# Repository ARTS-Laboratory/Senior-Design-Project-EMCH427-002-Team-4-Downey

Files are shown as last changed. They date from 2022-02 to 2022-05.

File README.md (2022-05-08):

# Senior-Design-Project-EMCH427-002-Team-4-Downey
## Camera-in-the-loop for Additive Manufacturing System (CLAMS)

### Background:
#### The Adaptive Real-Time Systems Laboratory (ARTS-Lab) at the University of South Carolina is working to develop a system for fault detection in additive manufactured components, particularly those that use metal-based processes.  Optical systems that can detect and quantify the size and location of the melt-pool in real-time are instrumental to this work.

### Project Purpose: 
#### This project will develop and build a camera-in-the-loop system that will include the camera housing, data acquisition system, and real-time computing hardware to compute the size and location of the melt pool. The software to compute the melt pool size will be provided but the project team will be required to implement this on real-time hardware. Key components to be developed include camera housing, data acquisition systems, real-time processing kernels, and display systems.

### Project Goal:
#### •	The development of a Camera-in-the-loop for Additive Manufacturing System. 

### Project Deliverables:
#### •	A fully functional camera-in-the-loop system.
#### •	A detailed public Github page will be made public and students can show it in their job search.
#### •	Detailed documentation with a “quick start guide”, source code, and CAD files. 

### Project Final Report:
#### •	The fianl report for the CLAMS.

## [Hardware setup for CLAMS](CLAMS_Hardware)
### 1. A build plate designed to accomadate monitoring apparatus
### 2. Camera mount to house optical camera
### 3. FLIR BFS-U3-16S2M-CS optical camera
### 4. Real-Time target unit
### 5. Display

concept individual components


## [Software](CLAMS_Software)
### Software designed during the development of this project.

## [Images and Figures](CLAMS_Images_&_Figures)
### Images and figures collected from this project.

## [Relevant Literature](CLAMS_Relevant_Literature)
### Documents including reports, research papers, user manuals, ect.

## [Source Code](CLAMS_Source_Code)
### Kernel and application code.

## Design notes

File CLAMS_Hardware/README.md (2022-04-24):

# CLAMS Hardware Setup

## [Custom Camera Mount](Custom_Camera_Mount)
### Drawings, G-code, and CAD files
2022-04-23 (3)

## [FLIR Optical Camera](FLIR_BFS_U3_16S2M_CS)
### Datasheet
2022-04-23 (4)

## [SLM Printer](Metal_3D_printer)
### Onwer's Manual


## [Monitor](Monitor)
2022-04-23 (7)

## [Real-Time Target Machine](Real_Time_Target_Units)
### User's Manual
2022-04-23 (6)

## [Return to Main Readme](https://github.com/ARTS-Laboratory/Senior-Design-Project-EMCH427-002-Team-4-Downey#readme)

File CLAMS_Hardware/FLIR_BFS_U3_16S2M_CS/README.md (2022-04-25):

# Flir Camera
## [Return to Hardware Readme](https://github.com/ARTS-Laboratory/Senior-Design-Project-EMCH427-002-Team-4-Downey/tree/main/CLAMS_Hardware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)

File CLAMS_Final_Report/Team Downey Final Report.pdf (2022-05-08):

## Adaptive Real-Time Systems Laboratory (ARTS-Lab)

## Camera-in-the-Loop System for Additive Manufacturing

## EMCH 427-428 – 2021-2022

Team Members: Malichi Flemming, Braden Priddy, Tyler Owens, Saif Wilkes-Davis

Industry Sponsor: Dr. Austin Downey

Department of Mechanical Engineering University of South Carolina Columbia, SC 29201

### Table of Contents

I. Executive Summary

The Adaptive Real-Time Systems Laboratory is a research group at the University of South

Carolina that does interdisciplinary research. They want a product that does monitors and

collects data on a selective laser melting printer for research of a Ph.D. candidate.

The needs of The Adaptive Real-Time Systems Laboratory were determined by doing several

interviews with Austin Downey and Yangzhou Fu and touring the printer, and after detailed

analysis, it was determined that light spectrum, speed of data acquisition system, speed of code

execution, detecting melt pool and quantifying melt pool were critical to satisfying those needs.

It was furthermore determined that a product to satisfy their requirements would need to be able

to process 200 frames per second, be portable, have a user-friendly repository of work, and able

to accurately and reliably generate contours with area calculations. It was thus determined that

the product mission should be the ARTS-Lab at the University of South Carolina needs a vision

system that can accurately track, calculate the brightness, and area of the melting sputters during

the SLM (Selective Laser Melting) process while functioning in real-time.

Given the above requirements, multiple concepts were researched and considered, as described

in this report. The ultimate concept selected to best satisfy The Adaptive Real-Time Systems

Laboratory’s needs was a FLIR camera with a bandpass filter in conjunction with a laptop for

storing and displaying data and Speedgoat controller as a real time target for Simulink code to

process the images. Details related to concept selection and subsequent product architecture are

supplied.

Speed of computational system, visibility of melt pool, and the accurate translation of brightness

to contours with area and locations are critical to functionality, and detailed engineering analyses are provided, demonstrating how expected light spectrum and heat transfer of the from the laser

to the PLA housing were modeled, under conditions of heat generated by the laser, and the

design was optimized.

Parameters included the camera’s execution speed, the melt pool’s light spectrum accuracy, and

the code’s processing speed are high priorities for production of the product. Therefore, the

design was optimized for these parameters which consisted of measuring how pixel size affected

processing time and analyzing individual functions in the code.

The prototype was tested by assessing different image processing methods to optimize speed and

the melting pool’s true area, displaying parameters versus not displaying parameters, and frames

per second versus the size of melting sputter under conditions ranging from optimal to non-

optimal.

Economic analysis of the scope of expenses associated with development of the prototype

indicate that, for a $24,253.40 investment, The Adaptive Real-Time Systems Laboratory will

recover all costs within the first unit sold and start earning profit at the same time.

II. Background

The Adaptive Real-Time Systems Laboratory is an interdisciplinary research laboratory at

the University of South Carolina. It is focused on developing tools and solutions that enable

systems (e.g., mechanical systems, aerospace structures, and civil infrastructure) to adapt to their

environments in real-time. It was created by and is led by Dr. Austin Downey, a professor at the

University of South Carolina in the Mechanical Engineering Department.

Digital twins will be a major factor for manufacturing in Industry 4.0 to increase reliability

by allowing real-time corrections to a process. The ARTS-Laboratory, in partnership with the

Metal 3D Printing Laboratory operated by Dr. Lang Yuan, is working to reduce waste by

increasing the accuracy and repeatability of the Selective Laser Melting 3D printer at the McNair

Center.

As part of the digital twin for this project, a computer vision system will be used to monitor

the performance characteristics of the printing process. With this data, Yangzhou Fu, a Ph.D.

candidate under Dr. Downey, will be able to apply a machine learning process to better the

additive manufacturing process with an in-situ system.

III. Customer Needs

3.1 Introduction

Determining customer needs accurately is critical to have a well-defined scope and a successful

project. Dr. Austin Downey of the ARTS Laboratory at the University of South Carolina needs

an in-situ monitoring system of a selective laser melting printer. With the guidance of Yanzhou

Fu, a Ph.D. student at the ARTS Laboratory, a computer vision system was created. This will be

used and tested in conjunction with the printer found in the McNair Center at the University of

South Carolina that is under the purview of Dr. Lang Yuan. One of the goals mentioned by Dr.

Downey was for the project to be useable by other research groups and hopefully industry

groups. Ultimately, the vision system needs to track the sputters, also known as molten ejecta,

created by the rapid heat of the metal powder. This project is designed to be one half of a digital

twin to do real-time corrections to SLM processes to improve the reliability to make it a more

accepted and viable practice.

3.2 Methodology

Dr. Downey and Mr. Fu were interviewed to understand what they wanted from the project. This

was done over the span of a few weeks to see if the goal would change based on the input.

Additionally, research was performed by watching Georgia Institute of Technology videos to

help understand what problem was being approached since this was a new concept. Additionally,

research was done to determine how the printer worked so it could be determined where the issue

in printing most likely was. The McNair center was visited with Mr. Fu to see the printer and its current setup. Afterward, discussions were had to determine what needs were most relevant via a

voting system.

3.3 Interpretation of Needs

Table 1: Original client needs

Needs Group | Needs | Needs #
Camera/Vision System | The system needs to be able to house the existing cameras and other future potential cameras | 1
| The camera mount must be stable. | 2
| The camera system must have a consistent field of vision. | 3
| The cameras must have appropriate frames per second to keep up the SLM’s scanner speed. | 4
| The cameras must have a proper light spectrum to view the part and the melt pool while the printing is occurring. | 5
| The camera must be protected | 6
DAQ/ Controller | The data acquisition system must be able to interface with available USB cameras as well as other commonly used USB camera systems. | 7
| The data acquisition system must be compatible with a real time system or fast enough to keep up with the cameras. | 8
| The data acquisition system must be cost effective. | 9
| The data acquisition system must be self-contained and portable. | 10
Code | The code must be executed fast enough | 12
| The code must be able to find the melt pool and outline the print area. | 13
| The code must be able to quantify melting pool area and sputters. | 14
| The code must track the x,y position of the melt pool | 15
| The code must have adequate documentation for future users. | 16
| The code must be able to display important parameters to the end user. | 17
Future Use/ Documentation | The system must come from existing equipment or 3D printed parts. | 18
| The system must have a repository for explaining how the system works. | 19
| The system must have a friendly GUI. | 20
| The documentation must be easy to use from technically literate people. | 21

Computer vision systems are made of several components such as image sensors, lens, vision

processor, communication interface, and lighting. The vision system consists of a camera and a custom holder to fulfill the image sensor and lens requirements. The data acquisition system

consists of a speed goat controller that handles the vision processing and communication aspects

of the design. Lastly, the lighting is created by the laser, melt pool, and plasma, and is filtered

using a bandpass filter. Each of the elements is broken out by subcomponent.

Needs Explanation:

1. The system needs to be able to house the existing cameras and other future potential cameras - To reduce cost, the use of existing equipment is a consideration.
2. The camera mount must be stable - To avoid vibrations from people walking nearby, the system needs to be held in place.
3. The camera system must have a consistent field of vision - The camera needs to see the same area in a repeatable fashion
4. The cameras must have appropriate frames per second to keep up the SLM’s scanner speed – The system needs to process frames at a set interval such that the distance the laser moves does not exceed a critical dimension length
5. The cameras must have a proper light spectrum to view the part and the melt pool while the printing is occurring – The camera must be able to see relevant aspects of the printing process
6. The camera must be protected - The system must be able to be reused for multiple other projects
7. The data acquisition system must be able to interface with available USB cameras as well as other commonly used USB camera systems – Dr. Downey has a FLIR USB camera that would be a preference for the system
8. The data acquisition system must be compatible with a real time system or fast enough to keep up with the cameras - The camera needs to see enough information fast enough to give accurate data on the melt process
9. The data acquisition system must be cost effective – Camera systems already exist, this system needs to save the ARTS laboratory money
10. The data acquisition system must be self-contained and portable – This product is a temporary addition to the SLM printer. It must be able to be removed and placed back again.
11. The code must be executed fast enough - The code must not prevent the camera system from achieving an appropriate speed
12. The code must be able to find the melt pool and outline the print area - The system needs a parameter to track for predictions later. By finding the melt pool and outlining it, it is possible to judge the consistency of the melting process and find deviations.
13. The code must be able to quantify melting pool area and sputters - The sputters, also known as molten ejecta, are a major source of defects in the printing process. Tracking their existence and size may make it possible to predict and eliminate them.

14. The code must track the x,y position of the melt pool - The code must be able to determine the location of the pool for reference of size later to improve the accuracy of the data by correcting locations relative to the camera
15. The code must have adequate documentation for future users – CAD and code must be available
16. The code must be able to display important parameters to the end-user - The end-user should be able to track the performance and correlate it to the printed quality.
17. The system must come from existing equipment or 3D printed parts – To save cost in a one-off prototype, the sponsor needs the part to be inexpensively made and customizable using resources available in the ARTS laboratory
18.  The system must have a repository for explaining how the system works – To make future work easier, code, instruction, CAD files, and other documents relevant to the project.
19. The system must have a friendly GUI – The end-user needs to be able to assess what is happening
20. The documentation must be easy to use for technically literate people- The end documentation must be accessible to those likely to use it

3.4 Prioritization of Needs

To determine the most important needs, a voting system [Table 2] was implemented. The

most important of the needs were given a four, the next most important given a two, marginally

important given a one, and the least important needs are given a zero. The total that must be

spent by each member is forty-eight.

Table 2: Point interpretation

Score | Interpretation
0 | Minimal Needed
1 | Marginally Important Need
2 | Mostly Needed
4 | Most Important
Must Spend | 48

Table 3: Affinity diagram

Needs # | Tyler | Malichi | Saif | Braden | Total | Rank
1 | 2 | 2 | 2 | 1 | 7 | 13
2 | 1 | 4 | 2 | 4 | 11 | 8
3 | 4 | 2 | 2 | 2 | 10 | 9

4 | 2 | 2 | 2 | 1 | 7 | 13
5 | 4 | 4 | 4 | 4 | 16 | 1
6 | 2 | 2 | 2 | 2 | 8 | 11
7 | 4 | 2 | 4 | 4 | 14 | 6
8 | 4 | 4 | 4 | 4 | 16 | 1
9 | 2 | 2 | 2 | 2 | 8 | 11
10 | 0 | 1 | 1 | 1 | 3 | 18
12 | 4 | 4 | 4 | 4 | 16 | 1
13 | 4 | 4 | 4 | 4 | 16 | 1
14 | 4 | 4 | 4 | 4 | 16 | 1
15 | 4 | 4 | 4 | 2 | 14 | 6
16 | 1 | 1 | 2 | 2 | 6 | 16
17 | 2 | 2 | 2 | 4 | 10 | 9
18 | 0 | 0 | 0 | 1 | 1 | 20
19 | 1 | 1 | 1 | 1 | 4 | 17
20 | 2 | 2 | 2 | 1 | 7 | 13
21 | 1 | 1 | 0 | 0 | 2 | 19
Individual Total | 48 | 48 | 48 | 48 | 192

Table 4: Top five results of first vote

Needs # | Tyler | Malichi | Saif | Braden | Total | Rank
5 | 4 | 4 | 4 | 4 | 16 | 1
8 | 4 | 4 | 4 | 4 | 16 | 1
12 | 4 | 4 | 4 | 4 | 16 | 1
13 | 4 | 4 | 4 | 4 | 16 | 1
14 | 4 | 4 | 4 | 4 | 16 | 1

Top Five Needs:

1. The cameras must have a proper light spectrum to view the part and the melt pool while the printing is occurring.
2. The data acquisition system must be compatible with a real-time system or fast enough to keep up with the cameras.
3. The code must be executed fast enough
4. The code must be able to find the melt pool and outline the print area
5. The code must be able to quantify melting pool area and sputters

Issue: While a top five was determined [Table 4], it was determined in the first round of voting

[Table 3]. This does not meet the requirements of a multiple voting process. There is a fair amount of overlap in the client's needs beyond the top five and the top five fail to consider the

full scope of the needs of the sponsor. Therefore, additional needs were generated by combining

other high-ranking needs and appending them to the top five. The most important needs after

modifications, voting, and discussions with the sponsor are seen below.

Vision System
1. The camera system must have a consistent field of vision - To make the product as reliable as possible, it is important that the edges of the images be consistent, so pixels represent the same space.
2. The cameras must have a proper light spectrum to view the part and the melt pool while the printing is occurring – For the system to work optimally, it is important to ignore extraneous sources of light.

Data Acquisition System
3. The data acquisition system must be self-contained and portable – This product is a temporary addition to the SLM printer. It must be able to be removed and placed back again.

Code
4. The code must be executed fast enough.  .5 ms (Allows for 200fps: Camera Max 226) -The system needs to track the rapid emissions of molten ejecta created by the laser heating process. The laser has a maximum travel speed of 2 meters per second. That means in one frame, the laser can travel up to 1 mm which may be a critical for tolerances depending on the application.
5. The code must be able to find the melt pool and outline the print area - The system needs a parameter to track for predictions later. By finding the melt pool and outlining it, it is possible to judge the consistency of the melting process and find deviations.
6. The code must be able to quantify melting pool area and sputters - The sputters, also known as molten ejecta, are a major source of defects in the printing process. Tracking their existence and size may make it possible to predict and eliminate them.
7. The code must be able to display important parameters to the end-user - The end-user should be able to track the performance and correlate it to the printed quality.

Future Use/Documentation
8.  The system must have a repository for explaining how the system works – To make future work easier, code, instruction, CAD files, and other documents relevant to the project.

### 3.5 Mission Statement

The ARTS-Lab at the University of South Carolina needs a vision system that can accurately

track, calculate brightness, and area of the melting sputters during the SLM (Selective Laser

Manufacturing) process while functioning in real-time.

IV. Specifications

### 4.1 Introduction

After the needs of the client were acquired over the course of several meetings with the

sponsor Dr. Downey and his Ph.D. student Yanzhou Fu. These needs went through three sets of

modifications as new information was exposed or issues arose. The list of client needs was

reduced to only the most vital 8. The needs were finalized after several rounds of voting using

scores ranging from 0-2.

After establishing and confirming the needs with the client, a needs metrics matrix was

crafted to help quantify the success throughout the project. Each of the client's needs is weighted

by importance based on the prior ranking of needs. For the needs metric matrix, a scale of 0, 1, 3,

and 9 was used. This was to emphasize items of utmost importance by using an exponentially

increasing ranking system adding more variance and preventing mass tying. The scale was in

ascending order of importance such that 0 had no importance and 9 had the most.

During this process, research was conducted to help generate specifications. Similar

research was found and used to find possible values for comparison. Most of the specifications

came from Dr. Downey and Mr. Fu. Beyond just setting specifications for the project to be

considered a success, fallback specifications were established to keep into account the wide

range of values that would arise as a result of the research-based environment of the project.

### 4.2 Metrics Table

Table 5: Metric table with target and fallback values

Needs | Units | Target specs | Fallback | Reference
Needs to detect melting pool (brightness) | Brightness | 0-255 | 0-255 | 3
Needs to detect melting pool (size) | Pixel value | Radius via contour | | 3
The cameras must have a proper light spectrum | Boolean | True positive | TP/TN | 6
Code must execute fast | ms | .5 | 33 | 3
Setup needs to be as compact and mobile as possible | cm^3 | 50 cm^3 | 100 cm^3 | 5
The code must be able to find the melt pool and outline the print area. | Boolean | True Positive | TP/TN | 5
The code must be able to display important parameters to the end-user | Boolean | True Positive | TP/TN | 5
The system must have a repository for explaining how the system works | Boolean | True Positive | TP/TN

Customer requirements/needs [Table 5] are in the leftmost column followed by the units used

to measure the need. Next are the target specs, which are the goals for the values attained. Fallback

values are acceptable values but not desired. Four client needs require true or false measurements, so

Boolean is the most often used metric for this project.

The idea of using a camera-in-the-loop system for detecting errors during an SLM (Selective

Laser Melting) process is a new idea that has been explored mostly by universities and research groups.

Because of the uniqueness of the idea, there are very few industry standards around the targets of the

project. Most of the target and fallback values are inferences made from other similar articles and

discussions with the project sponsors (Downey, Austin, and Yanzhou, Fu). These resources gave a good

idea of what the system’s target and fallback values should be in order to be successful.

### 4.3 Metrics Matrix

Table 6: Needs metrics matrix

The needs metrics matrix [Table 6] identifies the overall importance of each engineering

characteristic and ranks them in order of most important to least important. Out of the five engineering

characteristics, the most important has a ranking of one while the least important has a ranking of nine.

To determine these rankings, each customer need is assigned an importance weight factor from one to

five with five being the most important and one the least important. The table is set up to ascertain how

each engineering characteristic affects each customer requirement with values zero, one, three, and

nine representing a no, low, medium, and high correlation, respectively. From the results, it is

concluded that the Boolean metric ranks the highest, and the weight of the system ranks the lowest.

### 4.4 Outcomes

The client’s needs were taken and evaluated with the corresponding metrics and units using both

research and guidance from the project sponsors. After creating the two different tables above, a

clearer insight into the product's specific requirements was more readily attainable. Aside from the

Boolean metric, which is very generic, it was found that the two most essential engineering

characteristics were “the radius and brightness of the melting pool” and “processing time”. It was also

found that the “weight of the system” was the least necessary characteristic. The client requirement

that included the most engineering characteristics was the “the code must be able to find the melt pool

and outline the print area” with four correlations. The client requirement that included the least

engineering characteristics was the “the system must have a repository for explaining how the system

works” with one correlation. It was also determined the client's need with the most critical target and

fallback specification is the “need to detect melt pool (brightness)” and “code must execute fast” which

is appropriate, considering the two needs are the ultimate goal of the project.

V. Functional Concept

### 5.1 Introduction

The purpose of this chapter is to identify all functions of the vision tracking system.

Research was carried out on a variety of sources to develop a list of functions. From this list a

functional decomposition diagram was generated. A concept combination table was created by

researching and ideating a multitude of ways to execute each function. The Concept

Combination Table was then utilized to design five concepts that are applicable solutions for the

product. These concepts were analyzed and voted on to narrow down the options. These tools

were beneficial for understanding the problems that were faced and to develop a product that

fulfils the sponsor’s mission by choosing multiple solutions to answer these problems.

### 5.2 Functional Decomposition

A functional decomposition breaks down the product mission into detailed functions that

describe the problems that must be solved to build a successful vision tracking system. The

functions must consist of a verb and noun that answers the question, “what must this product

do,” to fulfill the product mission. Below is the detailed list of functions gathered for the

functional decomposition.

List of Functions
1. Locate Appropriate Camera Distance and Placement
2. Move Cameras into Position
3. Stabilize Camera System
4. Protect Camera from Heat, Molten Metal Sputters and Metal Powder
5. Operator determines Best Camera Settings
6. Set Camera Settings for Optimal Image Quality
- Set Camera to Correct Light Spectrum
- Set Resolution to Meet Image Quality Needs

- Set the Camera Frames Per Second to Meet Needs of Speed of the Printer
7. Accept External Energy from Power Source
8. Power Controller, Display, and Camera
9. Boot Real Time Operating System Initiating Tracking Program
10. User Inputs Command to Begin Tracking
11. Collect, Transfer, and Store/Buffer Images of Melting Pool from Camera to Data Acquisition System or Computer
12. Process the Images
13. Measure Radius and Luminance of Melting Pool

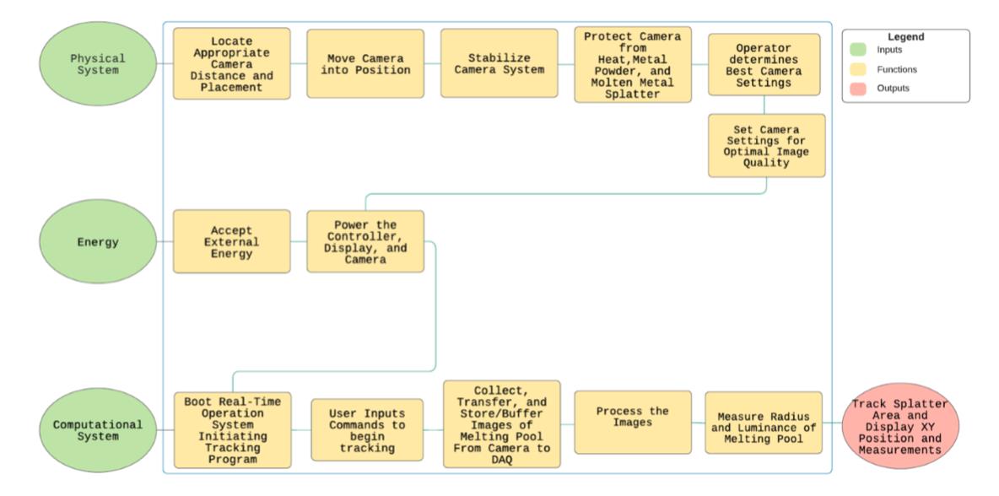
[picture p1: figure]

Figure 1: Function decomposition diagram

The diagram [Figure 1] functions as a visual representation of the required actions the

working product must implement to produce the desired outcome. The diagram consists of

inputs, functions, and outputs, flows primarily from left to right then secondarily from top to

bottom, and includes a color-coded legend for clarity. The inputs are the essential ingredients

needed to build the vision tracking system and the output(s) is the desired result of the fully

functioning product. The completed functional decomposition diagram can then be used to create

a concept combination table.

### 5.2 Concept Combinations

The Concept Combination Table (CCT) is a table that was generated using the functions

expressed in the Functional Decomposition Diagram. To formulate creative options, several

brainstorming and research sessions took place. In Table 7, each column of the CCT consists of a

heading that describes the function, and rows below containing all the feasible options that could

carry out the function.

Table 7: Concept Combination Table

Certain functions have only one logical option to fulfill it; however, additional options

were added for the sake of brainstorming and generating ideas. Functions such as “Boot the real-

time system” and “Move camera into position” would be done by hand. In principle,

accumulating these ideas assisted with future design concepts.

### 5. Concept Generation:

Concepts were generated by assigning one or more options from the Concept

Combination Table to each function and assembling the selected options into a viable concept.

Each team member assembled four concepts each totaling sixteen concepts, and the top five

concepts were chosen by vote. The following figures are illustrations of the chosen concepts

along with tables listing the technologies used for each function and brief explanations of how

the concepts work.

Table 8: Robot dog concept

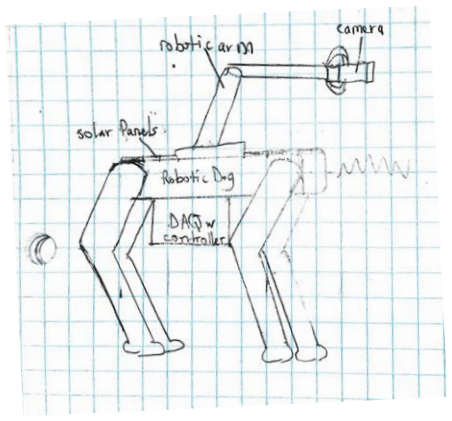
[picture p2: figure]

Figure 2: Robot dog concept hand drawing

In Figure 2, the Robot Dog concept uses a Boston Dynamic type robotic dog that is

powered by solar energy using solar panels placed along its back. The energy is stored in a built-

in battery that also powers the controller and camera. A robotic arm with a hand is attached to

the top of the robotic dog to hold, stabilize, and move the camera. A bright light-sensing camera

and C ++ software locate where to place the camera, sets camera settings, and processes the

images. The OpenCV function, calculate intersection(),a luminance meter records measurement,

and all data is stored on a hard drive disk. Desired output data is delivered via audio speaker

using text to speech application. Although the robot dog would be a creative idea, it would also

would very expensive, and solar power would not be effective indoors. Table 8 shows the

technology chosen for each function.

Table 9: Python application on laptop with SSK and heat-seeking camera concept

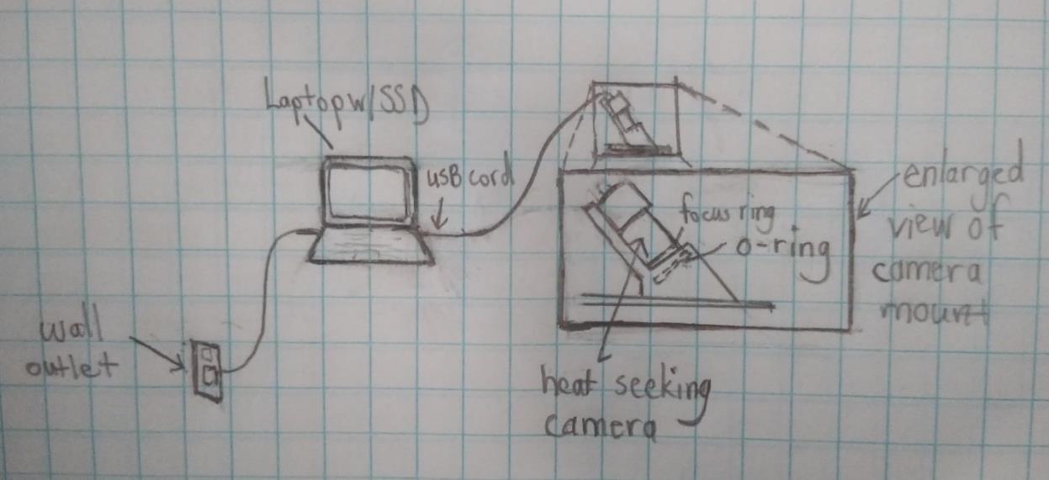
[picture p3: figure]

Figure 3: Laptop with SSD and Python concept

In Figure 3, a Python application that tracks the melting pool using a heat-seeking camera

will be executed on a laptop with SSD. The laptop is powered by a wall outlet and a USB cord

powers the camera and enables the transfer of data from the camera to the laptop. Focus rings

are manually added to focus the camera and a 3D printed camera holder with an O-ring stabilizes

and protects the camera. The laptop processes the data and displays the measurements on the

screen. This concept would be one of the most cost-efficient ideas and is the least complicated

which made it an ideal solution. Table 9 shows the technology chosen for each function.

Table 10: Robot arm with camera concept

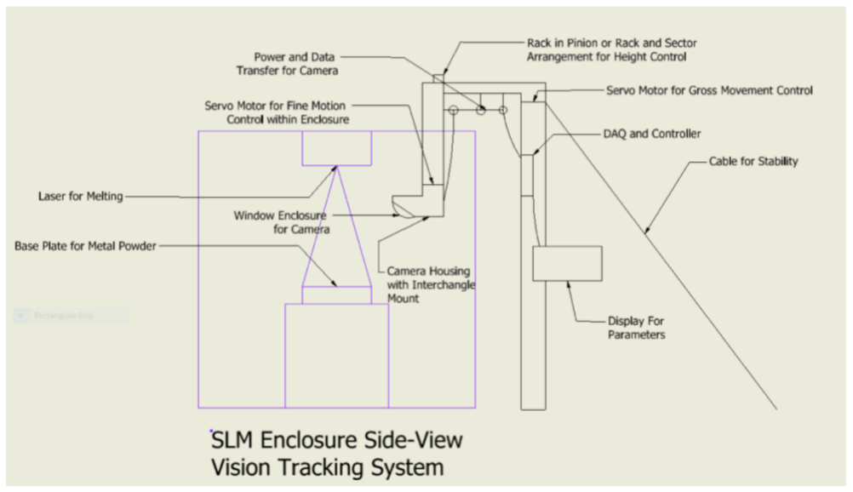
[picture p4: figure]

Figure 4: SCARA variant concept

In Figure 4, a robotic arm controls the positions of the camera within the enclosure. The

robot arm is designed to lift outside of the enclosure to allow for easy replacement of the

cameras as needed. The software takes into consideration the camera lens to determine the height

needed for optimal optics. To deal with the camera shaking during movements, a cable is added

to absorb some of the vibrations. A seal is formed with an O-ring and a 3D printed camera

housing to protect the cameras from harm. Power is supplied to the display, controller, and

motors from a 120 Volt outlet. The controller then powers the camera system. Once powered, the image will be processed in a real-time operating system running Python code. This code tracks

luminance to determine the melt pool position and splatter patterns.

This design is good because it can manipulate the camera into better angles than the

current mounting setup. The overall setup is inexpensive. The pole could be made of PVC or

wood and the motors harvested from equipment at a state surplus. The rest of it could be 3D

printed. Unfortunately, the complexity of the design would add more work to the project and add

cost to Dr. Downey. Additionally, it would need a secondary controller for the motor system.

Table 10 shows the technology chosen for each function.

Table 11:Manual control of system

Figure 5: Manual control of system

In Figure 5, the system is controlled primarily by the user. The camera is manually

adjusted using focus dials, and the user is holding the camera in the necessary location. The

camera is a heat-seeking camera therefore the printer has an open area to let heat out. However,

the user and the camera should not get overheated, so a fan is placed in the vicinity for cooling.

The user is also wearing a battery pack that is powering the system. Data is displayed on the TV

screen. This option is optimal for being able to control the system to the users' liking, however,

that means there must always be someone there during use. Table 11 shows the technology

chosen for each function.

Table 12: Remotely viewed data

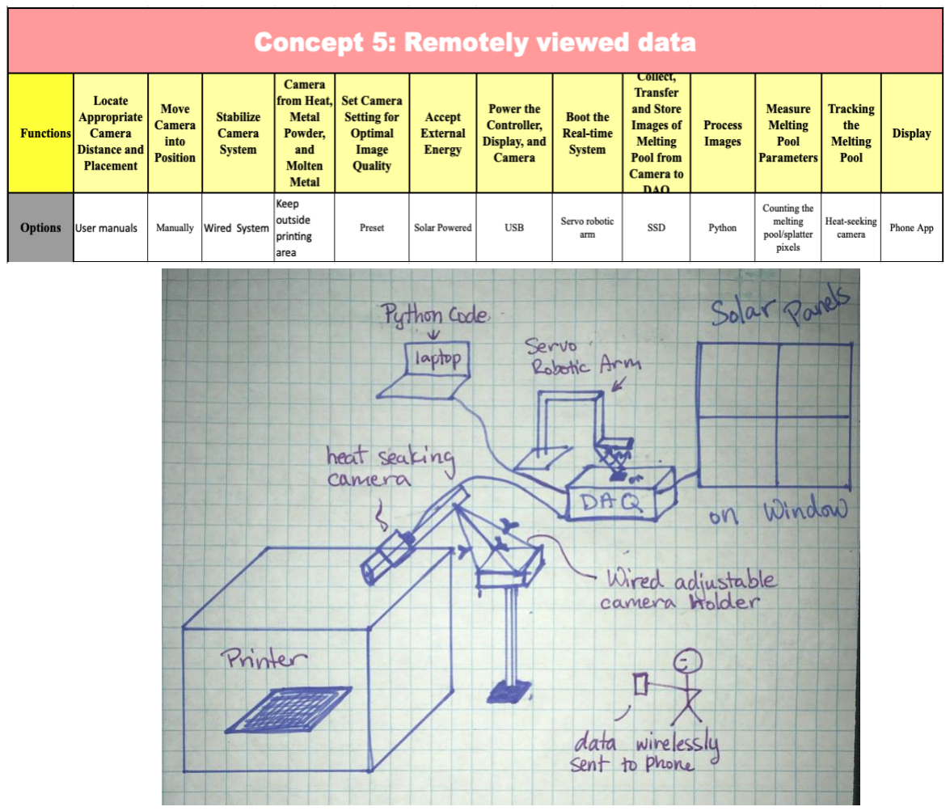
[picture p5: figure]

Figure 6: Remotely viewed data

In Figure 6, the camera is set up outside the printing area and held in place using an

adjustable wired setup. The system is booted using a remote-controlled servo arm and everything

is powered by solar panels attached to a nearby window. The data is configured using python

code and then wirelessly sent to the user’s phone via a cellphone application. The wired setup is

convenient since it can be adjusted to fit the apparatus, however, having data sent wirelessly to a

phone app gives opportunities for security violations. Table 12 shows the technology chosen for

each function.

### 5.3 Research performed

Patents were searched for under a couple of websites - Google patents [7] and United States

Patent and Trademark Office [8]. Keywords include the following:

- Metal 3-dimensional printer monitoring
- 3-dimensional printer monitoring
- 3-dimensional printer tracking
- Melting pool tracking
- Melting pool monitoring
- Monitoring of laser powder bed
- Selective laser melting
- Melting pool measurement
- Melting pool parameters
- Metal powder bed monitoring
•
There were few relevant patents to consider that were found using the above keywords

and that are cited in the appendix of this report. The first being the “Method and System for

Monitoring Additive Manufacturing Processes” [9] which is an invention that teaches quality

assurance for additive manufacturing using a multi-sensor and a real-time quality system.

Similarities include using multiple optical sensors to monitor the powder bed and using a real-

time operating system.

Another patent that is related to the project is one titled “Printer monitoring” [10] and is a

system that monitors 3D printers using a baseline image to compare to future images taken to determine the status of the print job and alert the user of any failures. This patent is not, however,

used with metal 3D printers, but collecting images to track data is similar to the project.

The last patent that was found that pertained to this project is the invention titled

“Procedure and apparatus for in-situ monitoring and feedback control of selective laser powder

processing” [11] which monitors and controls the Selective Laser Powder Processing by using a

scanning device to follow the laser beam as well as a detector that can capture electromagnetic

radiation emitted from movement on the powder surface. It also consists of an optical system to

follow the laser beam.

The idea of using a camera-in-the-loop system for detecting errors during an SLM

(Selective Laser Melting) process is a new idea that has been explored mostly by other

universities and research groups. As such many of the ideas rely heavily upon other journals of

other research groups.

The research article “Machine-Learning-Based Monitoring of Laser Powder Bed Fusion”

[12] was very constructive for the concept generation. This article is like what is being

accomplished in the project and has helped generate quite a few new options for the functions.

One idea extracted from this article is the use of angled mirrors to get a top-down view of the

metal powder bed [Figure 7].

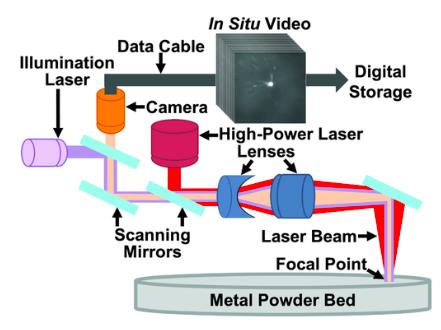
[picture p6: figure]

Figure 7: SLM video process

This idea can drastically simplify the project in two ways. With the use of mirrors, there is no

concern about varying camera angles and positioning; effectively eliminating two of the

functions (1. Locate Appropriate Camera Distance and Placement and 2. Move Cameras into

Position).

One important need of the sponsor is the software aspect. The product needs to be able to

track the 3D printing process and display the melting pool parameters all in real-time. This can

be difficult to code completely from scratch, so other ways to simplify this process were

researched. One way that was found was to use the OpenCV library [13]. Open Computer

Vision, “is an open-source computer vision and machine learning software library... that provides

a real-time optimized Computer Vision library, tools, and hardware [13].” OpenCV helped

generate options for two of the functions. The first function “12. Process the Images,” is done to

extract useful information from an image by modifying it. This can be accomplished almost exclusively by OpenCV functions. The image can be processed by multiple functions like

cvtColor(), GaussianBlur(), threshold(), erode(), and dilate(). All of which help the code find the

parameters of the melting pool. The second function OpenCV helped generate options for was,

“13. Measure Radius and Luminance of Melting Pool.” As shown in Figure 8, OpenCV has a

handy function called grab_contours(), which can draw a border around the melting pool.

Figure 8: Contour around the melting pool

Once this boundary is set, the melting pool’s parameters (centroid location, area, and radius) can

be calculated.

### 7. Conclusions:

All the designs share the project sponsor’s requirement that currently owned cameras

were used. This was important because there was a limited budget. Due to the nature of the

printer, it was important that the cameras were protected from heat and molten metal splatters.

One similarity between designs was that the camera was either outside of the printer enclosure or

protected with a casing if it was inside the enclosure.

One design limitation considered was that it needed to minimize the amount of human

interaction or manual work because there was not a budget for labor. Furthermore, there was

limited knowledge of robotics systems among the team working on the project so avoiding

complex solutions was necessary. Additionally, security concerns were considered because of the potential for confidential images of prototypes being made. The most complex functions to

solve were processing images or collecting and transferring images. This was because the coding

element for processing the images was successfully achieved in Python but needed to be

implemented in real-time.

VI. Concept Selection

### 6.1 Introduction

Project design is a strenuous and complex process for any engineering project. To

alleviate the difficulty of design selection, a variety of brainstorming methods were employed

which produced a multitude of designs. The brainstorming process began by listing the sponsor’s

needs to establish the desired parameters and a budget limit. Then the required functions of the

final design were listed, and a Functional Decomposition Diagram was constructed to help

illustrate how the design would work. For each of the functions, an extensive number of options

were produced. From these options, seven different designs were conceptualized enabling the

initiation of the Concept Design Review process. The first part of the process, Concept

Screening, involved narrowing down the concepts and deciding which ones could be combined

to create an optimal design concept. After narrowing down the seven concepts to three, the

second part of the process, Concept Ranking, began. Each of the three concepts were ranked by

weighing the sponsor’s needs to determine if the concepts could satisfy the design functions.

### 6.2 Concept Screening

Table 13: Initial concept screening

The selection criteria used for the concept screening were created and later updated after

meeting with the project sponsor. The criteria were adapted from the sponsor’s needs list as well

as the concepts that were designed. The concept screening [Table 13] was done by comparing the

reference concept, the original design endorsed by the sponsor, with the six novel concept

designs. The following symbols were used to rank the designs: a negative sign ‘-’ to represent

the design’s failure to meet the criteria as sufficiently as the reference design, a positive sign ‘+’

to represent the design successfully exceeding the reference design in meeting the criteria, and a

zero ‘0’ to represent the design matching the reference design’s ability to meet the criteria. The

reference design was given a zero for each of the criteria to provide a base level. The purpose of

using this type of concept screening was to rule out any designs that were not actually feasible

and to give the team an opportunity to take positive concepts from designs that didn’t rank very

high as a whole and piece them together to create a new combined design. The outcome of this concept screening took the team from the original 7 designs to 3 designs that include a

combination design.

### 6.3 Concept Ranking

Table 14: Final concept ranking

The concept ranking [Table 14] took place after determining the weights of the selection

criteria, a process that can be seen in the appendix. The criteria were compared to each other and

given a score of 1, 3, 5, 7, or 9 with a ranking of 1 having the lowest level of importance and 9

being much more important. Concept #2 (the reference concept) was the final selected concept

with the highest ranking. This was mainly due to the low budget available, and the simple setup

required. However, because concept #8 ranked so closely with the reference concept, a

discussion with the sponsor took place.

### 6.4 Final Concept

The final concept selected was concept #2, the reference concept, which is a python

application that tracks the melting pool splatter using an optical camera and executes on a laptop with a solid-state drive. Powered from a wall outlet, the laptop is then connected to the heat-

seeking camera via USB cable to power the camera and transfer data from the camera to the

laptop as seen in Figure 9.

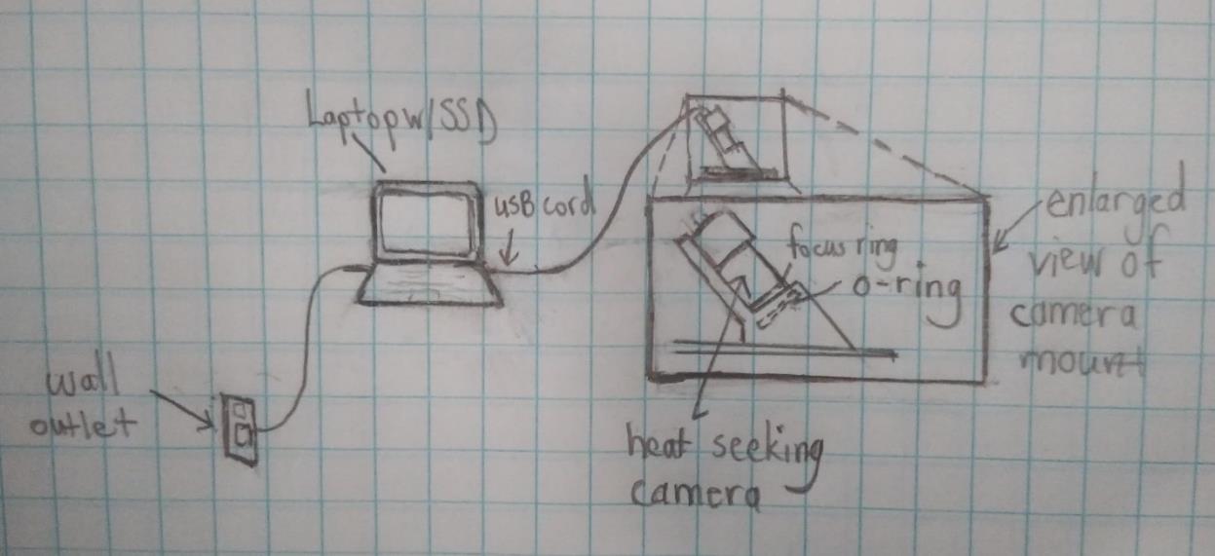
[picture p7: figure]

Figure 9: Laptop with Solid State Drive and Python Concept

The camera is held and protected by a 3D-printed camera mount with an O-ring and

focused on the printing bed area using focus rings as needed. After the laptop processes the data,

the data is displayed on the screen. Challenges with this concept included designing a camera

mount that can be adjusted for cameras of various sizes and shapes or capable of holding

multiple cameras that can gather data synchronously. Finding a DAQ with the ability to process

data from multiple cameras in real-time proved to be challenging as well. However, using

different types of cameras simultaneously to find a greater diversity of data could be

advantageous. Furthermore, just gathering data in real-time was a difficult task. As the

development of the project began, the final design was bound to change. However, these changes

were nothing but a small speed bump in the development process due to the work put into the

Concept Design Process.

VII. Product Architecture

### 7.1 Introduction

Creating the project architecture report is a process that is used to break down the

functional elements into groups or clusters that can help define the systems of the project. The

benefit of this process is it introduced new elements that were not previously considered. Two

new clusters were added to the functional decomposition diagram which included the digital and

processing aspects of the system.

### 7.2 Product Layout

The layout below in Figure 10 consists of five clusters total. The five clusters are the

Camera Unit, Control Unit, Digital System, C++ Code, and User HMI (Human Machine

Interface). The first cluster, the Camera Unit, contains all functions pertaining to the physical

setup, positioning, and protection of the camera and camera mount. The second cluster, the

Control Unit, contains all functions needed to operate the real-time vision tracking system such

as the power supply, real-time operating system, all data flow functions, and tracking code. The

third cluster is the Digital System which is embedded within the Control Unit cluster. This

cluster demonstrates how the data flows from the camera to be stored, is processed, and ran

through the code to obtain the desired splatter measurements. The fourth cluster, the C++ Code,

describes how the code will analyze the received data to calculate the area, radius, and brightness

of the splatter. This cluster is embedded within the Digital Systems cluster. The last cluster is

the User HMI which contains all functions that require human interaction such as manually

setting camera settings, inputting commands to the operating system, and receiving output data.

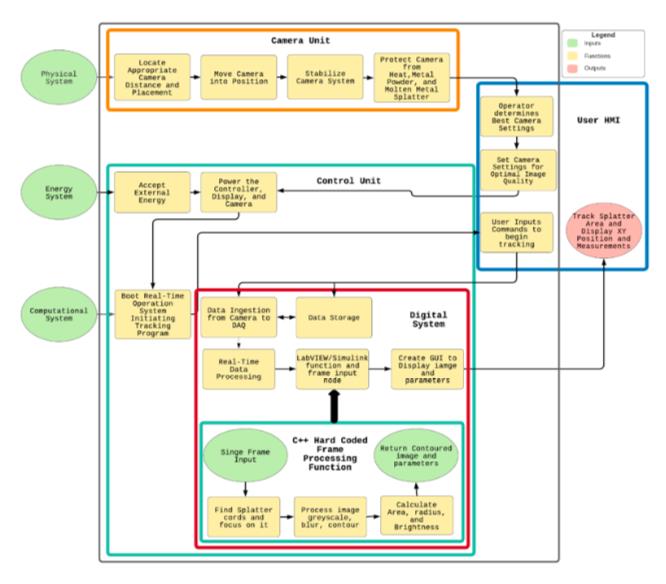
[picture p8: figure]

Figure 10: Real-time vision tracking system functional decomposition diagram with clustered functions

### 7.3 Interactions

Below is a list of interactions or interruptions that could occur while or before the system

is running. After the interaction is stated there is a proposed solution to avoid the problems that

could occur.

a. The operating system interrupts the process for the code to collect data.
- Run a real-time operating system to limit the number of OS interrupts
b. Stack overflow
- More RAM
- Faster and Deterministic processing
- Real-time or Stream processing
c. Non-optimal drivers’ compatibility could cause slower communication speed or prevent the camera from communicating with the computer system.
- Build it or find it
d. Vibrations of someone walking near the camera could interrupt the accuracy of the tracking.

- Keep people away
- Add a soft rubber mount to absorb vibrations (Also makes it airtight)
e. Camera distance consistency could cause out-of-focus pictures and an inconsistent field of vision in the area of interest, which will affect the ability to convert pixels into area consistently.
- Always mount flush
f. Frame losses could result in inaccurate tracking.
- Better network protocols
- Better Drivers
- Better processors
- More RAM
g. Bandpass lets too many wavelengths in like a laser which won’t let the user see the melt pool or other areas of interest.
- Review bandpass characteristics
- Buy more
h. The heat bed gives off infrared radiation which could affect picture quality.
- Avoid thermal cameras
- Avoid long wavelengths in bandpass filters
i. Code Speed could cause inadequate frames per second which would cause significant loss in data.
- Faster processor
- Switching from Python to C++
- Changing where information is stored and called
- Change structure and functions used
j. Slow bus speed will overwhelm the system and cause more data loss.
- Purchase a faster computer of at least PCI 2.0

### 7.4 Geometric Layout

For the geometric layout, a CAD model [Figure 11] was created to represent how the

physical system is laid out. Below, a metal 3D printer is used in conjunction with the already

manufactured camera holder in orange that fits securely into the upper window on the printer’s

frame. The camera is shown in the camera holder and will be sealed with an O-ring. The camera

will be connected to the controller, and the controller will be connected to a laptop. In Figure 12,

the graphical model is shown with the corresponding data flow.

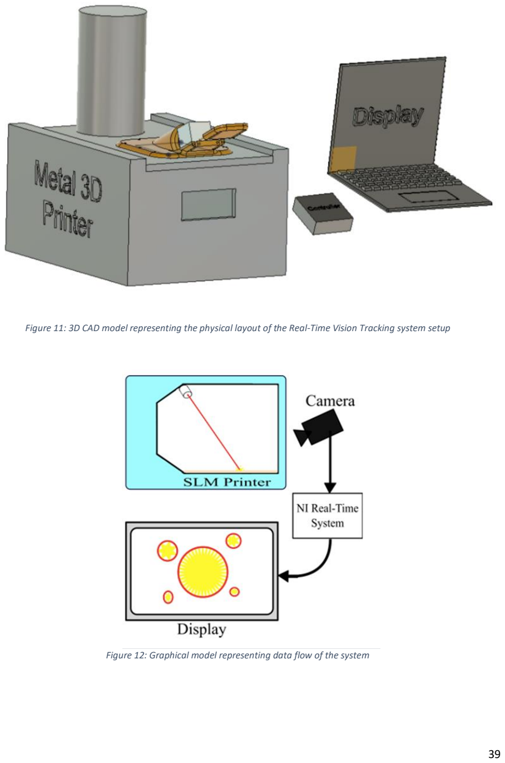
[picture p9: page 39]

Figure 11: 3D CAD model representing the physical layout of the Real-Time Vision Tracking system setup

Figure 12: Graphical model representing data flow of the system

VIII. Engineering Analysis

### 8.1 Introduction

Team Downey was asked to create and implement a vision tracking system for a selective

laser melting (SLM) printer in the McNair Center. Ensuring that the system has the fewest errors

possible is imperative to allow the sponsor to move forward to the next steps of the project. The

issues that have the potential to get in the way of reaching this target include not reaching the

real-time goal, inaccurate sputter parameter data, an unclear picture produced from the camera,

and a deformed camera housing from excessive heat exposure. The camera housing unit will be

evaluated using thermal analysis via Fusion 360 and with the known properties of the PLA used

to print the part. Ensuring the real-time goal is reached can be done by evaluating the

computation time inside the code. The optical issues are avoided with the proper filter and the

angle that the camera sits at. These parameters are calculated using the focal length and field of

view equations, and the wavelength selection.

### 8.2 Analyses Performed

Analysis #1 - Thermal
Analysis performed:

The thermal analysis of the camera housing was performed using Fusion 360 a

CAD software. With a laser temperature of 500 °C, the SLM process might seem too

extreme to use a PLA 3D printed part as a camera mount. However, the measured

temperature at the point of contact between the camera housing and the metal 3D printer

averaged only 38 °C when tested. This information was then put into a CAD thermal

simulation for analysis.

For thermal analysis of PLA material, the melting point temperature is not a

principal factor because deformation of the material begins prior to reaching its melting

point. It is the glass transition temperature of PLA, which is the point at which the storage

modulus begins to decrease [Figure 13].

Figure 13: Temperature vs. Storage Modulus of PLA

The storage modulus measures the elastic response of a material. During this

phase, the amorphous material begins to lose rigidity as it transitions from a solid and

slightly brittle state into a rubbery and glass state. The glass transition temperature, the

temperature at which PLA will begin to deform, is between 50°C and 80°C. Therefore,

the temperature in contact with the camera mount should stay below 50 °C to ensure the

camera will stay in the intended place and undamaged.

Modeling/Analysis results:

Below in Figure 14, the temperature is analyzed throughout the camera housing.

With the bottom face of the object receiving an applied thermal temperature of 38°C and

the top faces being exposed to room temperature of 20°C, the maximum temperature is

37.8 °C, and the minimum temperature 31.58°C.

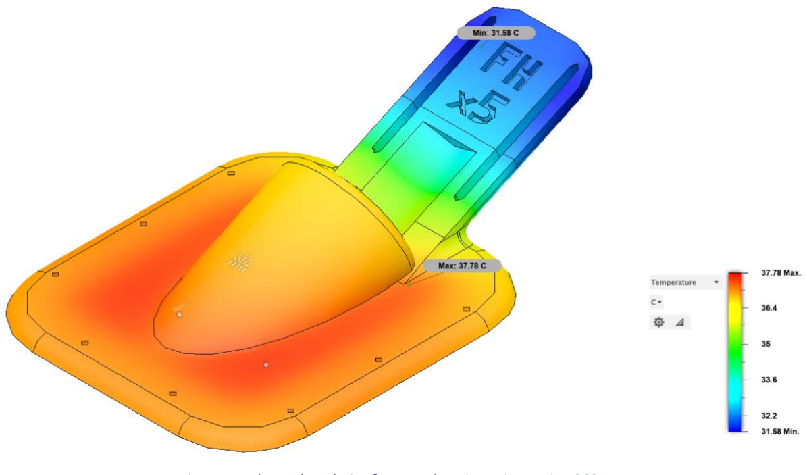
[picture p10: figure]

Figure 14: Thermal analysis of camera housing using Fusion 360

Analysis #2 – Computation Time
Analysis performed:

The most essential part of the system is that it must be implemented in real-time. In software

terms real-time is defined as, “Real-time programs must guarantee a response within specified time

constraints, often referred to as "deadlines".[20]” To accomplish this goal, all the digital parts of the

system need to work on the same timing schedule to ensure that there is no buffering in the output

display and data collection. There are two types of deadlines in real-time computing, hard and soft.

In soft deadlines, if a deadline is missed the system will not fail and the result can still be used.

However, the longer the system runs the bigger the buffer becomes. For example, if the end-user

were watching the output video feed thirty (30) minutes after the start of the system they could only see what was happening five (5) minutes ago which would make a soft deadline system not useful.

In hard deadlines, the system will fail, and no data can be collected if the deadline is missed. This

real-time system adheres to a hard deadline because the input data comes from a video feed that can

go on for hours.

30 FPS
1 sec
≈ 30ms | Equation 1

To ensure the software meets the hard deadline, the computation time of the program is matched to

the video input frames per second (fps). [Equation 1] shows the approximated deadline to process

each frame as it comes in. To determine if the code meets that deadline, two different timing

functions will be used for each language the program is currently coded in. “Linux time” will be

used for the C++ version, and “time.process_time()” will be used for the Python version since both

find the total user CPU time of the code.

Modeling/Analysis results:

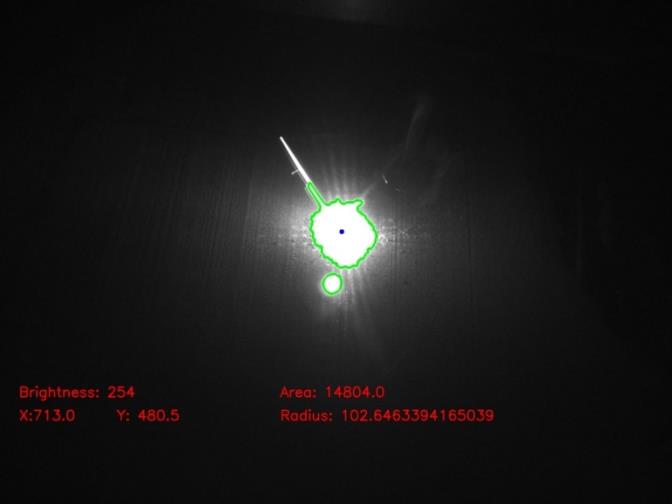
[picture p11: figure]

Figure 15: Test Frame

The user CPU time for the C++ program to process one frame of the video was 15 ms

which met the hard deadline with ease. The user CPU time for the Python program to process

one frame of the video was 28.6 ms. This is cutting it fairly close to the proposed deadline of

30ms and could potentially cause problems in the future. In the test frame used for each program

[Figure 15] there are two contours that were found, one for the melting pool and a smaller one

for the sputter. If the program processed a frame with multiple sputters, the processing time

would increase and potentially lead to a system failure. This factor suggests the Python version

will not suffice and implementing the C++ code should be initialized instead.

Analysis #3 - Optics

Analysis Performed – Thin Lens Equation:

Based on the CS-Mount information provided the distance from the sensor to the lens is

12.5mm. This is used in conjunction with the assumed distance to the print to find the focal

length. This is an important characteristic for optical properties.

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
Equation 2

Where f is focal length, u is distance from lens to sensor, v is distance from lens to object

Table 15: Focal length calculations

Assumed Distance to Print (mm) | Focal Length (mm)
50 | 10
75 | 10.71428571
100 | 11.11111111
125 | 11.36363636
150 | 11.53846154
175 | 11.66666667
200 | 11.76470588

Analysis Performed – Field of View Calculations

The calculations are based on the focal length, sensor dimension, and field of view. To

find depth of field f-number of the camera in operation is needed which is unknown.

Table 16: Linear field of view calculations

Assumed Distance to Print (mm) | Linear Field of View (Width in mm) | Linear Field of View (Height in mm)
50 | 24.84 | 18.63
75 | 34.776 | 26.082
100 | 44.712 | 33.534
125 | 54.648 | 40.986
150 | 64.584 | 48.438
175 | 74.52 | 55.89
200 | 84.456 | 63.342

Figure 16: Optical performance of camera based on wavelength

Analysis Performed - Wien's displacement law

Derived from blackbody radiation and its maxwell distribution which is dependent on temperature.

wavelengtℎ peak =

B
T

Equation 3

B – Wien's displacement constant - 2.897771955×10⁻³ m⋅K T – Temperature

Table 17: Dominate Wavelength at a given temperature

Temperature of Melted Steel (C) | Wavelength (nm)
2000 | 1274.783
2100 | 1221.066
2200 | 1171.693
2300 | 1126.157
2400 | 1084.029
2500 | 1044.939
2600 | 1008.57
2700 | 974.6471
2800 | 942.9322
2900 | 913.2162
3000 | 885.316

Note: This ignores the effect of plasma in the imaging process. Also, the typical temperature of

the melted steel is around 3000 C.

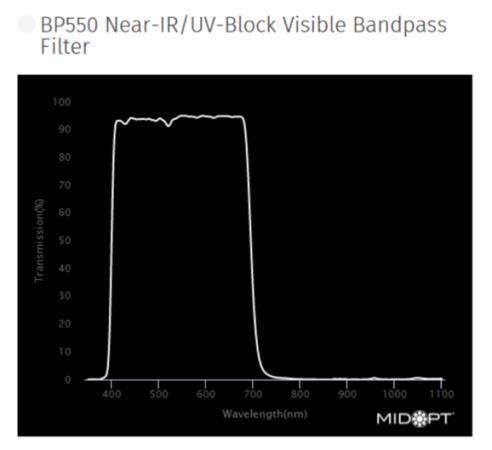
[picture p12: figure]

Figure 17: Bandpass filter

This filtering was selected based on a research paper that talked about the wavelength emitted by

the laser during the melting process, so it eliminates the noise created by the surrounding area

being heated by the melt pool. Additionally, there is an angle when viewing the print so it will

experience skewing which will impact the data being collected and analyzed.

### 8.3 Conclusions/Recommendations

After these analyses were performed it was concluded that the camera housing will not

deform due to extreme heat since the analyzed temperature stays below the glass transition

temperature. It was concluded that the code would be able to run in real-time and lastly, the

camera would be able to be positioned correctly with the right dimensions provided. And, from

the preliminary tests Python may be risky to move forward with. Instead, the next step was to

work on implementing the C++ code to meet the hard real-time deadline.

IX. Manufacturability

### 9.1.1 Design for X

Introduction:

After analyzing the materials and functionality of the overall system being produced, the next

step is to review the design to safely manufacture and assemble the system for future use. A

successful way to analyze the system for refinement is to implement the “Design for Excellence”

system known as DFX. Among the given manufacturability, assembly, cost, and safety

parameters, other parameters will be recognized during the design refinement. One of the added

parameters is an encouraged prerequisite knowledge in the programs used in the system which

will aid in the ease of future use. Design for real-time usage is implemented from previously

established sponsor needs. Finally, public access is a parameter that was requested through the

sponsor and is fulfilled in the new design.

Design for Manufacturability and Assembly:

The system is made of two custom designed pieces to allow visibility into the printing

chamber and then a computer vision system. The first designed piece is a replacement for the

standard lid that covers the print area and seals the system. The second piece is a housing unit for

the camera. In terms of what is needed for each of these parts, the first must allow camera access

to the print area without impacting the printing process and the latter must hold the camera stable

and have a seal to prevent gas or metal powder from leaking into or out of the print chamber.

To replace the existing lid, a new plate would need to be turned into a lid with a viewing

port. Two candidates for material would be steel or aluminum. Because aluminum is cheaper,

lighter, easier to machine, and strength of material was not a factor, it was the obvious choice for

this task. An alternative to aluminum would be any series of corrosion-resistant steel such as 316

Steel because the melting pool ejecta could solidify onto the lid and cause corrosion attacks

resulting in pitting due to dissimilar metals and it is stored in a non-dehumidified room.

For creating the plate, aluminum can be cast, forged, or extruded then milled to

specifications. The procurement of the plate was done by the University of South Carolina

machine shop and subsequently milled. Please note, most of this was done prior to working on

the project.

For the housing unit, any material would have been acceptable if it was strong enough to

hold the camera, remain rigid at above room temperatures, cheap to replace and the part can be

built quickly with said material. Polylactic Acid (PLA), a thermoplastic, was selected for several

reasons. The first was it was readily available in the ARTs Laboratory. The second is that its

glass transition temperature is around 60-80 degrees Celsius which is higher than the predicted

maximum temperature the housing will be exposed to.

An alternative that would also be inexpensive and still in the realm of 3D printing would

be using a lithographic-based resin printer. The resin option would allow for dealing with greater

temperatures with the added benefit of greater dimensional accuracy and finish. The biggest

drawbacks of this are the toxic fumes from the resin and the availability of this type of printer to

the sponsor. This may be a better option should a seal be deemed necessary for the product or if

PLA begins to deteriorate from exposure to the metal printing.

There is yet another benefit to working with the 3D printer. As the scope and product get

tested, there is flexibility to adjust the design and iterate an enhanced speed via skipping a

machinist or ordering an existing part and waiting for shipping. The product needs to have some

flexibility to change as the sponsors need. This method best allows the creation of different

housing modules to accommodate different cameras down the road should that be needed. There were several iterations of the camera housing. The angle of the camera was changed several

times. To accommodate the change in angle, a support structure was added as the cylinder

holding the camera shifted. Additionally, modifications to the slot for the camera were made.

One such change was the landing spot for the camera lens to fit against an O-ring.

The remaining items for this project are screws and hardware related to the computer

vision system. These are modular pieces that can be interchanged with related products. For

example, any USB-3.0 camera could work with the setup. Additionally, more I/O can be added

for monitoring things like bed temperature with thermocouples which is another consideration

for this project.

The end assembly of the product involves lining up the housing unit with the modified lid

and screwing in screws to their corresponding threaded holes. The corners of the print chamber

line up with the lid making finding the holes in the print chamber easier with less time spent on

the guesswork of positioning. Additionally, for the entire product assembly, wires must be run

and connected to their corresponding I/O. There still is a need to investigate the airtightness of

the 3d printed housing unit and the aluminum plate.

The last step of getting the product operational is the deployment of the code for the

computer vision system. The code is stored on Git-Hub to allow access to it anywhere via the

internet. Additionally, all support documentation for the project including the camera housing

file is available in the repository to help avoid confusion.

Design for Cost:

To minimize costs, it was necessary to find the best software and hardware that met the

needs of the project and was the least expensive. On the hardware side, equipment was needed

that was easily transportable, modular, compatible with the software, and fast. An X1 Extreme

ThinkPad was chosen for the brains of the system because it’s a durable laptop with plenty of power and speed. The ThinkPad is very cost-friendly in caparison to its piers with similar

performance capabilities. The fast and compact Speedgoat real-time unit system aids in the

modularity of the entire system, and its integration with MATLAB/Simulink significantly

decreases the cost for data acquisition. The Speedgoat eliminates the need for a controller/chassis

system that is far more expensive, larger, and more complex to use for real-time applications.

The selected method of creating the housing unit was fused filament fabrication. This was

primarily chosen for convenience and cost. The ARTs Laboratory already houses multiple 3D

printers. An Ender-3 pro was used, and the geometry of the part allowed for minimal support

material to be used saving time and money. An alternative to this choice would be to take an

aluminum block/billet. In terms of cost, the block is not expensive ranging from 30-50 USD,

however, it requires greater than 3-axis machining so the cost would increase since the part has

complex geometries and overhangs of a circular nature. By not going the metal housing route,

time and money would be saved. The part prints in under 24 hours without much supervision or

intervention. A skilled machinist would have to devote time and energy to replicating the

geometries and tolerancing the 3d printer can already achieve. eBay was used to find the

hardware needed at the lowest cost. On the software side, MATLAB/Simulink was chosen

because it is less expensive than software such as NI’s LabVIEW. It’s perfect for real-time

applications, especially vision-based projects, and is easy to use. For future production, a

universal camera housing would be needed but was not necessary for this project.

Design for Safety:

There are multiple safety factors involved in this project, but all are easily controlled by

implementing the recommended precautions. The metal 3D printer will include the most safety

precautions, and all are listed in the printer’s manual (Appendix) which would need to be read through before use. The system’s area includes the proper exhaust and circulation along with the

necessary fire extinguishers: A-B-C-extinguishing agents for fires caused by electricity, sand, or

D-extinguishing agents for fires of processing materials. Flame retardant gloves, full respiratory

mask with category P3 filter, and powder protective glasses are on-site and will be highly

recommended in the systems manual. Flame retardant gloves, full respiratory mask with category

P3 filter, and powder protective glasses are on-site and will be highly recommended in the

systems manual. The design of the camera housing was created with no sharp edges and little to

no safety hazards. The electronics will be placed on top of cooling fans to avoid overheating. The

milled cover is made of aluminum and is light enough for the average person to be able to handle

it with ease.

Design for “Speed”:

The purpose of this project is to produce an accurate real-time system that can eventually

be used to detect errors in an SLM process. The goal is to hand off this system to the sponsors:

Austin Downey and Yanzhou Fu, who will implement a machine learning model that can learn

from these errors. For a machine learning model to be able to learn from data a lot of processed

data is needed while maintaining a high degree of accuracy.

The most important requirement of the project is the real-time aspect of the system. To

reach the real-time deadline, the image processing code needs to be able to process a frame from

the video feed before the next frame comes in. Over the course of the last two months, different

versions of the same image processing code for C++ and Python were developed and optimized

to reach the real-time deadline. This code will then be implemented onto a real-time system

(Speedgoat or PXI-8812) with the use of either LABVIEW or Simulink Real-time.

One major drawback to writing the code with C++ is that it is a difficult language to use

and implement. There are many little things that can go wrong when setting up OpenCV libraries

and this would be required for every user to do. The next design focuses more on the ease-of-use

aspect.

Design for “Accessibility”:

Another important aspect of the project is accessibility and ease of use. The goal is to

make this system as accessible as possible. This is reflected in some of the design choices. The

camera frame can be 3d printed, making it accessible to any university or company that wants to

implement the system. Simulink Real-time is used instead of LABVIEW. LABVIEW

subscription is more costly than a MATLAB subscription. The code will be written in MATLAB

because the code needs to be compiled with Simulink in real-time. While working with other

coding languages in Simulink is possible. There is an initial setup required by the user before

they can implement the code.

Conclusions:

Key refinements in the process were the implementation of MATLAB/Simulink in

conjunction with the Speedgoat DAQ. This combination reduced the cost on the hardware end

and software end significantly. It also increased the overall speed capabilities of the real-time

vision application with integrated real-time modules that are easy to program and implement.

The system is easy to assemble, calls for minimal manufacturing and maintenance, efficient, and

safe. Ideally, recommended future changes could be made to the camera housing to allow for

various camera adaptations and the ability to change the angle of focus.

### 9.2 Build instructions

Introduction:

This report will provide the necessary instructions for future users to easily set up and

operate the system. A detailed list of all materials needed is provided in the appendix along with

the links to access the necessary g-code and Python code.

Setting up the code:

The code is the foundation of the project, it is what connects all the components of the

system together. The primary need described by the sponsor was to have the system work in real-

time (in this case under 30ms). The same frame processing code was written in three different

languages (Python, C++, and MATLAB) to see how well each performed and was implemented

on a real-time machine.

A. Download the chosen programing language and get acquainted with the platform.
B. Download the chosen program of either Simulink or LabVIEW.
C. Download the supplied Python code from the publicly accessible GitHub account using the following link. GitHub. (https://github.com/ARTS-Laboratory/Senior-Design-Project-EMCH427-002-Team-4-Downey)
D. The utilized Python code can be seen in the screenshot below (Figure 1). Code comments describe how the frame is processed, how the sputter parameters are found, and, can be used to better understand the process.

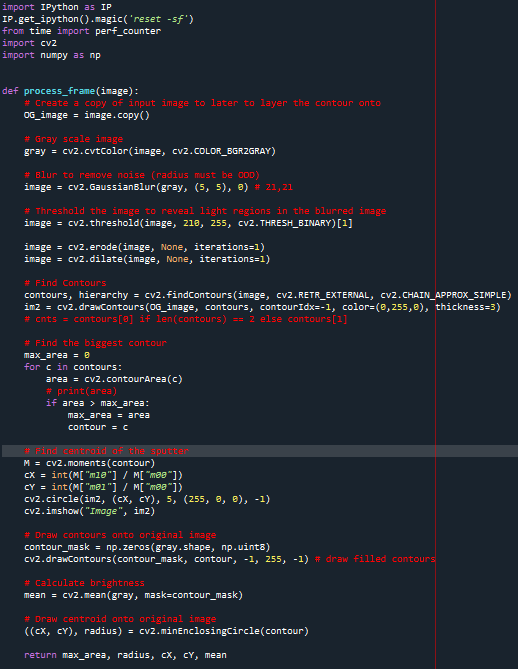
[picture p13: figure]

Figure 18: Screenshot of Python code supplied by GitHub

E. To implement the frame processing code onto the Speed Goat real-time unit, either LABVIEW real-time or Simulink real-time will need to be used. Below (Figure 2) shows the general process to implement the code in Simulink with the code placed into a MATLAB function block.

Figure 19: MATLAB function block

F. To completely understand the history and process of this project, there is a general read me in the GitHub repository which describes what the project is about, how it is implemented, and answers to basic troubleshooting problems.
G. Once the code is implemented onto the Speed goat it will be ready to be deployed.
H. The code is set up so that it is user-friendly and can be started with just the touch of any key on the keyboard of the laptop in use.

Preparation of the Ender 3 Creality 3D printer:

A. Clean the printer bed thoroughly by removing any leftover remanence of PLA from any previous prints.
B. The bed should be leveled manually by adjusting the four leveling springs below the bed to acquire equal, paper-thin spacing between the extruding nozzle and the surface of the build plate.
C. The PLA should be loaded into the printer following the instructions from the printer’s manual (Appendix).
D. The temperature settings for the build plate and the nozzle should be set at 60° F and 210° F [Figure 20].

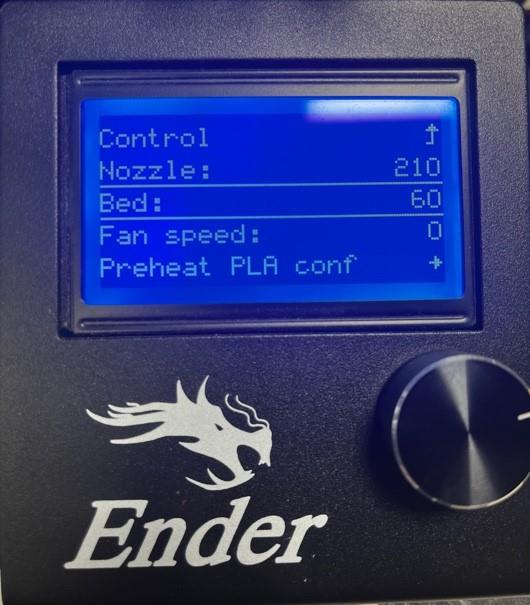
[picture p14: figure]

Figure 20: Temperature setting for 3D printer

Note: A small test print is highly recommended before attempting to print the camera housing.

Printing the camera housing:

A. Access to the g-code for the camera housing can be found on the public GitHub account for this project using the link below: https://github.com/ARTS-Laboratory/Senior-Design-Project-EMCH427-002-Team-4-Downey/tree/main/G-code (https://github.com/ARTS-Laboratory/Senior-Design-Project-EMCH427-002-Team-4-Downey/tree/main/G-code)
B. The type of filament used to print the camera housing is 1.75 mm diameter MakerBot PLA filament [Figure 21].
C. Place filament onto material rack.

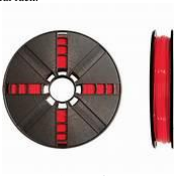
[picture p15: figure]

Figure 21: MakerBot PLA filament

D. Preheat the nozzle temperature to approximately 210 degrees.
E. Press the extrusion spring, and feed filament through the extruder until it reaches the nozzle opening.
F. Print the camera mount at 100% speed.
G. Download g-code files from GitHub onto a microSD card.
H. Insert microSD card into microSD card port of 3D printer.
I. Power on 3D printer.
J. Scroll down to the ‘Print From TF’ command and select.
K. Scroll down to ‘camera mount part A’ and select to print first section of camera mount.
L. After first section is complete, select ‘camera mount part B’ to print second section of the camera mount.
M. Remove parts with care and discard any support sections.
N. Using an adhesive, bond the four studs of camera mount part B [Figure 23] into the four holes of camera mount part A [Figure 22].

Figure 22: CAD drawing of part A

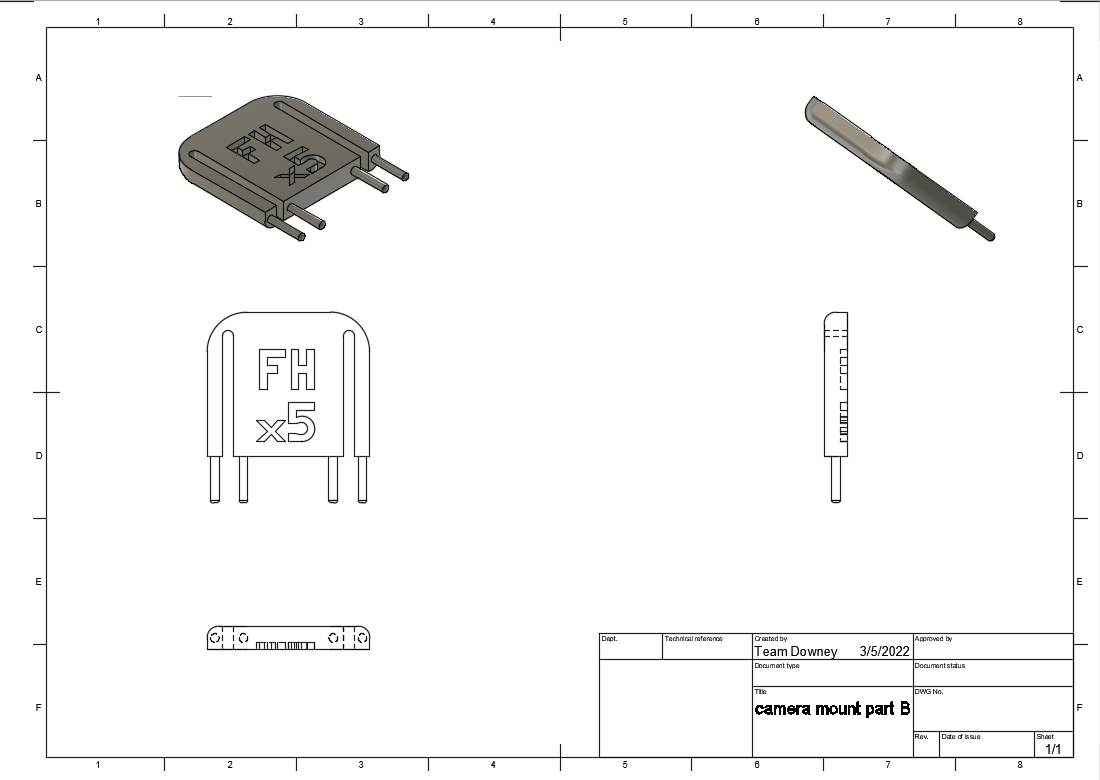
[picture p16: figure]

Figure 23: CAD drawing of part B

Camera Settings:

A. Install FLIR Spinnaker support by Image Acquisition Toolbox using the instruction provided at https://www.mathworks.com/matlabcentral/fileexchange/69202-flir-spinnaker-support-by-image-acquisition-toolbox (https://www.mathworks.com/matlabcentral/fileexchange/69202-flir-spinnaker-support-by-image-acquisition-toolbox) and Spinnaker SDK at https://www.flir.com/products/spinnaker-sdk/
B. Set white balance of the camera using a thick piece of white paper to avoid shadows from bending
C. Enable auto exposure and check the quality of imaging of the printing process. The exposure can be manually controlled to help focus on the desired target more effectively. The camera is under-exposed if the histogram of the light intensity distribution is negatively skewed. The opposite is true for over-exposure.
D. Control the exposure time, gain, and gamma until the brightness of the laser and melting no longer overwhelm the CMOS sensor in the camera.
E. Adjust the image format until it meets the desired area and resolution needed for the zone of interest

Setting up the metal 3D printer with aluminum lid and camera housing:

A. The previously milled and assembled aluminum lid is placed onto the metal 3D printer using the handles to maneuver [Figure 24]. Mount flush with the back wall of the lid holder. It should fit securely in the opening of the 3D printer. The circular opening of the lid should be pointing towards the back of the printer and the square opening towards the front. Close the telescoping housing for the laser to ensure proper placement of the circle.

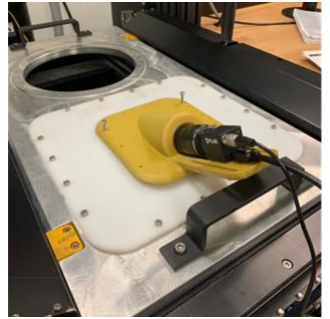
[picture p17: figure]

Figure 24: View of aluminum plate with camera housing

B. The camera housing will fit securely into the square opening with the elongated camera rest facing the front of the printer [Figure 24].
C. Secure camera housing corners to the lid using four M4 machine screws [Figure 25] with an Allen wrench.

Figure 25: M4 machine screw

D. O-ring will slide into its built-in compartment in the opening of the camera housing [Figure 26].

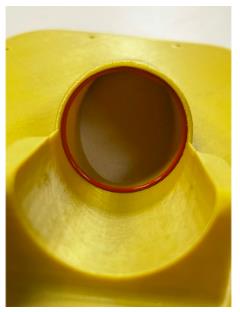
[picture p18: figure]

Figure 26: O-ring inside camera housing

E. The camera with camera lens already attached should get placed in the camera housing lens first. The camera body will rest on the elongated section of the camera housing and the lens will fit securely against the O-ring. Ensure from the left-hand side FLIR is in the correct orientation. If it is upside down, flip the camera 180 degrees. If it is not visible, rotate 90 degrees and check the orientation.

Connecting all elements:

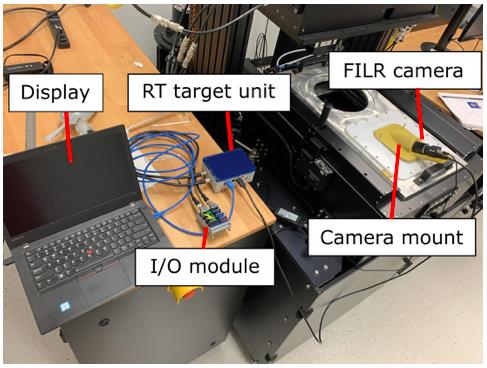
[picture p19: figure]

Figure 27: Connections between camera and DAQ

A. The PLA camera mount is first screwed onto the lid of the SLM printer
B. The FILR camera is then secured into the camera mount.
C. The Camera is connected to the Speed Goat real-time target unit via a USB 3.0 cable.
D. The unprocessed frame data is first sent to the I/O module from the data input to translate analog or digital signals to a digital value.
E. Then the digital data is sent back through the data output so the Speed Goat can begin to process the frame data.
F. The frame processing code is hardcoded onto the Speed goat system, so the code does not have to compile each run.
G. The processed frame is then displayed on a ThinkPad laptop connected by an ethernet cable and the sputter parameters are saved to a database on the laptop.
H. The hardware should be near the SLM printer on a sturdy table that won’t be in an area that could be in any way disturbed.

Running the system:

A. User will press any key on the keyboard on the display laptop to start the data collection
and the processing of frames
B. A read me found on GitHub using the following link GitHub (https://github.com/ARTS-Laboratory/Senior-Design-Project-EMCH427-002-Team-4-Downey) describes general problems that may occur while code is running. For example, if the code is running before the SLM process is started there will not be a sputter pool to detect and calculate the parameters, resulting in an error.
i. Troubleshooting the problems while testing code on the Speed Goat real-time unit will be difficult and time-consuming. Speed Goat itself will not display errors. Instead, the error would have to be replicated on the computer using the same inputs that caused the error on the Speed Goat. In order to save time troubleshooting, the code needs to be perfect before implementation on the Speed Goat begins.
C. The display [Figure 28] gives the user the following information:
i. A photo taken using the FLIR camera.
ii. | An outline of sputter created.
iii. | The brightness in lumens.
iv. | The area of outlined splatter.
v. The x and y dimensions. vi. The radius of sputter outline.

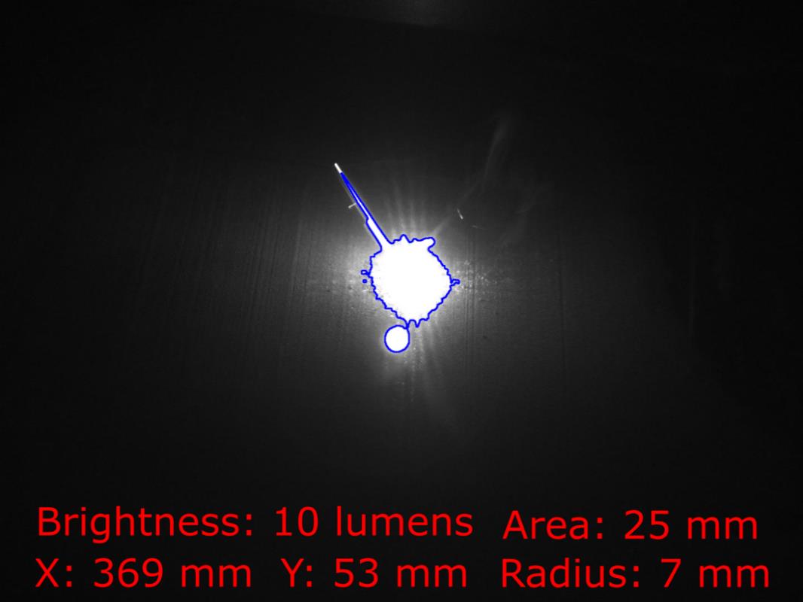
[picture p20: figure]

Figure 28:The programmed results display

Maintenance:
A. This system needs to be stored and operated in a low humidity, climate-controlled environment. Left in the heat or elements, PLA (the camera housing’s material), degrades becoming brittle and with the potential biodegrading as well. The aluminum lid is exposed to other metals via the powder and molten ejecta in the print chamber, creating the potential for a galvanic cell if exposed to moisture. Electronics, including the camera, are also sensitive to humidity especially if it is high enough for condensation to form.
B. The system should be periodically cleaned.
i. The lenses of the camera system should only be cleaned with compressed air, avoid canned air, as most cloth materials could accidentally cause scratching.
ii. | In the event of handling the lenses, use untextured nitrile gloves to avoid
| getting oil or contaminates of the lens.
iii. | The material used to clean the lens should be a cotton swab or a lint free. This
| would be especially noticeable on the filter lens as abrasions will degrade the
| filter's ability to block light. Should the filter lens become overly damaged, UV
| light could begin to degrade the CMOS sensor causing more noise and
| eventually making it unusable.
iv. | Care should be taken to avoid using solvents to clean the lenses of the camera
| system as well.
v. The camera should be stored in a cloth bag inside of a cardboard box.
vi. Exposure to sunlight should be avoided.
C. Keep the PLA camera housing clean to avoid the presence of the metal powder because it is highly volatile.
i. Avoid acetone, ethyl acetate, methyl ethyl ketone, tetrahydrofuran and sodium
| hydroxide as they readily dissolve PLA.
ii. | Using compressed air, avoid canned compressed air.
iii. | If a solvent is needed, Isopropyl alcohol is a preferable option to clean it. The
| alcohol should evaporate readily and not oxidize the potential metal powder
| unlike other common cleaning products like bleach. Allow several minutes for
| the evaporation of isopropanol before reassembly to avoid alcohol vapors in
| the laser chamber.
D. The aluminum lid should be cleaned periodically to remove any metal powder that may contaminate the surface.
i. Use a cloth, disposable wipe to remove powder from the surface.
ii. | Take care to use compressed air on threaded holes that cannot be cleaned well
| with the wipe. It is important to clean these screw holes because they are
| another source of potential issues.
iii. | Isopropanol can be used if a solvent is needed.
E. Care should be taken to minimize the strain on cables.
i. Give the cables adequate slack.
ii. | Avoid large bending moments near the connectors.
iii. | Do not jam the connectors if they do not fit, this will result in damage.
iv. | It may be necessary to add a strain relief grommet to increase the longevity of
| the cables.

v. Cables should be wound into about 4-8 in wide circles depending on their lengths for storage to avoid overstraining.
F. The computer, I/O module, and real-time target for the system should be kept in a climate-controlled environment like an office and not inside of the room where the printer is located. This is to minimize exposure to metal powder during the loading process prior to the print beginning.
G. The computer and real-time target should be cleaned with compressed air after every use in the SLM printer room to avoid the powder from possibly shorting the systems.

## X. Economic Analysis

### 10.1 Introduction:

Economic analyses are necessary for projects that are used for both profit and non-profit

purposes. The nature of this project is primarily research-based with almost no startup cost and a

heavy emphasis on being available to the general public at no cost. Because of this unique

situation, a hypothetical economic analysis was performed with the revenue and lifespan of the

product as if it would be used for profit. The estimations that were used for this analysis had

been either researched using similar products or discussed with the project sponsor. This

economic analysis considered initial start-up costs, labor from the technician operating the

system, cost for maintenance, and demand and revenue of the project if sold for profit.

### 10.2 Costs, Savings, and Revenues

Summary of costs, both up-front and recurring:

All materials that will be needed to run the product are listed below [Table 18]. This does

not include the SLM printer or sliding aluminum cover since both are outside the scope of this

project. These materials make up most of the cost to build a unit.

Table 18: Bill of materials

Part | Qty | Price ($)
ThinkPad X1 Extreme | 1 | 4,077.98
Ender 3 3D printer | 1 | 251.99
PLA | 1 spool | 22.99
Simulink software license | 1 year | 1,300.00
MATLAB software license | 1 year | 880.00
Camera FLIR blacklfy USB | 1 | 1,887.00
Bandpass filter | 1 | 67.50
O-ring silicone | 1 | 7.92
Speed goat controller | 1 | 9000.00
Machine screws | 4 | 8.00
Total | | $17,503.40

Client time:

a. Sponsor -1.5 hrs per week x 30 weeks at $83.00 per hr [30]
b. Consulting Engineer/Technician - 1.5 hrs per week x 30 weeks at $50.00 per hr. [31] Recurring costs:
a. MATLAB yearly license renewal fees - $880.00 [32]
b. Simulink yearly license renewal fees - $1,300.00 [32]
c. Utilities or non-reusable materials- No use of power that was previously done manually or expendable materials that weren’t previously needed. Total cost is listed in Table 19.

Table 19: Upfront and repeating costs

| Cost | Time | Total
Sponsor | $83.00 | x 1.5 hrs x 30 wks | $3,735.00
CE/Technician | $50.00 | x 1.5 hrs x 30 wks | $2,250.00
MATLAB | $880.00 | x 5 yrs | $4,400.00
Simulink | $1,300 | x 5 yrs | $6,500.00
Total | | | $16,885.00

Summary of Savings:

A. Savings on labor:
i. Technician manually track melting splatter- $66,000 per yr [33]
ii. Technician manually measure and document melting splatter dimensions and brightness frame by frame- $66,000 per yr [33]
B. Output increase:
i.Increased output due to accelerated fault detection capability- It would be impossible to determine how much the output would increase because the size and complexity of the part being printed could vary significantly.
C. Maintenance cost savings: i.Since the vision system would have no effect on the SLM printer directly, there would not be any maintenance cost savings.
D. Production cost savings: i.Although there would be production cost saving, it is impossible to determine due to the variety of parts that could be printed. Total savings are listed in Table3.

Table 20: Product benefits

| Savings | Time | Total
Melting splatter tracker | $66,000.00 | x 5 yrs | $330,000.00
Melting splatter measurer | $66,000.00 | x 5 yrs | $330,000.00
Total Savings | | | $660,00.00

### 10.3 Analysis

Cash Flow Diagram

A cash flow diagram is used to visualize the incoming and outgoing cash throughout the

project’s life. In Figure 29 it is shown how this project will have an incoming flow of cash after

its first year on the market. To analyze the products cash flow further the net product can be

found by establishing the revenue, operating costs, gross margin, annual depreciation charge,

taxable income, income tax, and net income after taxes [Table 21.]. The depreciation charge can

be calculated using the equation 4.

Depreciation =

initial cost−salvage value number of years

Equation 4

Figure 29: Cash flow diagram

Table 21: Annual cash flow with taxes

Revenue (1 year) | $200,000.00
Operating costs | $44,006
Gross Margin | $155,994
Annual Depreciation charge | $4,382.00
Taxable income | $151,612
Income tax (39%) | $59,129
Net income after taxes | $92,483
Net cash flow (after taxes) | $96,865

### 10.4 Break even analysis

In order know the point at which the product will start being profitable, a break-even

analysis is performed [Table 22]. This project will break even after its first unit is sold which is

ideal for a solid business plan. The formula to find the break-even point is below in equation 5.

Break even point =

Fixed cost
Margin per unit

Equation 5

Table 22: Break even analysis

Break Even Analysis
Startup Costs | $24,253.40
Sale Price Per Unit | $100,000
Units/Year | 2
Profit/Unit | $77,997
Profit Margin | 78%
Units to break even | 1
Days to break even | 180
Profit/Year (before taxes) | $155,994

A more visual representation can be seen in graph form [Figure 30] where the grey line

represents the total cost over 5 years, the orange line represents cash inflow, and the vertical blue

line represents the break-even point which is where the total cost and revenue intersect.

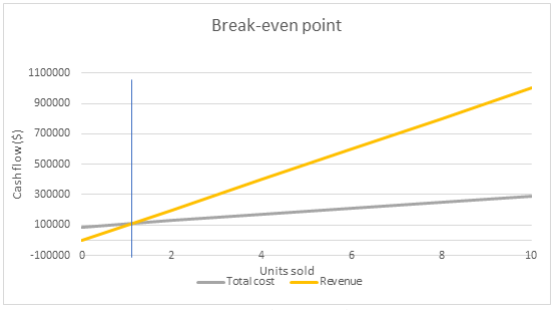
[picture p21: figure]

Figure 30: Break-even point graph

### 10.5 Profitability analysis

To gauge the profitability of a project and the potential return expected, it’s important to

find the net present value (NPV) or the internal rate of return (IRR). This project’s NPV was

analyzed using equation 6 below.

NPV = ∑

Rt
(1+i)

t

T
t=1

Equation 6

Rt is the net cash flow, t is time of cash flow and i is the discount rate. For this analysis the

discount rate is assumed to be 10%. This gave a total NPV of $342,942 [Table 23]. The IRR can

be found using equation 7.

NPV = 0 = ∑

Rt
(1+IRR)

t

T
t=1

Equation 7

Here the NPV is set to zero and the IRR is calculated. This can be difficult to do manually and is

simplified by using the IRR Excel function which is what was done to find the IRR in Table 24.

However, it is noted that value given from Excel, 199%, is quite large and this could be due to

the large profit margin.

Table 23: Net present value analysis

Net Present Value
| Project Time (years) | 5
| Discount Rate: | 10%
Year | Present Value
0 | $-24,253
1 | $88,059
2 | $80,054
3 | $72,776
4 | $66,160
5 | $60,146
Total Net Present Value (NPW): | $342,942

Table 24: Internal rate of return (IRR)

Project Time (years) | 5
Internal Rate of Return | 199%

### 10.4 Summary

Cost and Profitability

With an estimated revenue of $100,000 per unit sold and two units sold per year by Dr.

Downey, the cost of the product, $24,253.40, will be covered fully within the first purchase and

be profitable ever year afterwards. It is marketable with projected savings of customers being

over half a million dollars per year in labor alone and is one of the first systems available for monitoring metal 3D printing. Every year, there is an estimated profit of around $155,994 for the

project sponsor. In the span of five years, the net present worth of the project will be $342,942.

Additional Benefits

In terms of impact on the market, this is one of the first computer vision systems for

metal 3D printing. It will improve the output of metal additive manufacturing by allowing

operators to view and stop a print if defects are detected before wasting more time and material

continuing a defective print. Eventually, it will be used for real time control of the metal 3D

printing process to prevent and avoid defects via a digital twin setup which will make the process

more robust, making it a better option for manufacturers. This will allow for new geometries to

be implemented that subtractive manufacturing is unable to handle with a similar quality and

reliability. Furthermore, with a more robust process, ASME can recognize it and implement

standards for those seeking to use it. An example of this would be for heat exchangers in

pressure vessels like boiler systems. By having new geometry options, new advances can be

made to transfer the heat. This also would apply to computer chips as well. Include discussion of

any intangible or less-quantifiable benefits

Computer vision as a means of real time correction will be a major industry overhaul

during Industry 4.0. Reducing waste, increasing consistency or quality, and adapting to the

manufacturing process are all important to making the best product. 3D printing, in particular

metal 3D printing, is plagued with minor inconsistencies which can range from minor visual

blobs to internal void defects that severely weaken the materials compared to a wrought metal.

The benefit of this project is many folds. First, it will be used in a digital twin setup for U of SC

for a PhD Student enhancing his education with an innovative concept that is in its infancy in now. Additionally, it will spawn multiple papers regarding machine learning and additive

manufacturing bolstering the reputation of U of SC.

XI. Product Testing

### 11.1 Introduction

Product testing is critical to verify the system's functionality and assess its limitations.

Data must be acquired through experimentation, processed for error mitigation, and analyzed for

results. For this product, the following parameters were evaluated: consistency and speed of the

operating system, camera’s field of view and placement, most efficient processing method, and

accurate measurements. The most rigorously tested parameters were the consistency and speed

of the operating system because they fulfill the most essential requirement for real-time image

processing.

Since real-time systems are defined by hard deadline times, the system would fail if these

deadlines weren’t met. Henceforth, most of the testing focused on optimizing the code and the

system, as well as testing the limits of the code.

Despite the end product not being functional due to a hardware malfunction of the Speed

Goat, the project was a success overall. The code for the system meets the required timing

deadline and processes a SLM video on a Speed Goat Real-time Unit. To demonstrate the

functionality of the code, a prototype was assembled using a test setup, laptop, and a USB

camera. The prototype produced a processed image and a file containing splatter parameter data

on a live feed at 30 fps. The last step to completing the product is finding and configuring a

Speed Goat compatible camera.

### 11.2 Test Plan

Due to limited access to the SLM printer laboratory, the construction of a rudimentary

model of the SLM printer was required to conduct adequate experimentation. The model was

comprised of a cardboard box, the plastic plate where the camera housing is seated, and a

Styrofoam ball to imitate the metal splatter. A square hole was cut out on the top of the box

which allows the camera housing to fit securely with the plastic plate and for the camera to view

inside the box. A circular hole was cut out at the opposite end of the box as an area for the

splatter replica to be suspended from. The inside of the box was painted black, and the splatter

replica was painted bright green and illuminated with a flashlight to mimic the light contrast.

Test #1

Testing individual function processing times.

Throughout most of the coding process, only one frame was being processed to see if it met the

sponsors’ real-time deadline of 30 milliseconds. One way this can be analyzed is looking at

individual functions within the code to see which has the greatest effect on processing time

[Table 25]. This gives an idea of what to focus on when optimizing. This test was done multiple

times throughout the design process. This test is the final function time analysis test of the

completed code.

Table 25: Function time analysis of a single frame

Calculating the sputter area, radius, and centroid take up the greatest percentage of the

processing time. These calculations are done using the MATLAB function “regionprops”, very little was done to optimize this as calculating the radius and centroid is difficult. The next most

expensive function is the “variable and RGB image initialization”, this cannot be optimized

further as the minimum number of variables is already used. The last function that takes a large

percentage of the processing time is the “draw contours and calculate the brightness”. This can

be optimized by no longer drawing the contour around the image, but this eliminates visual

aspects of the display which tells the user that the sputter is being found by the code. The reason

this function takes so long is that the code must go through the entire sputter pixel list to

calculate the brightness.

Test #2

Testing frames per second vs the size of melting sputter.

The code must calculate the brightness and the contours of the main sputter. As the sputter gets

bigger the more pixels will have to be gone through to calculate these parameters. For this test, 5

white squares of increasing size show how each affects the processing time [Figure 31]. From

this test, the limits of the code were visualized. The code must work at 30 fps and the processing

time needs to work under 33 milliseconds.

Figure 31: Five 1440x1080 images of squares

Figure 32: Processing time vs. area

Table 26: Processing time vs. area of squares

| Area | Processing Time
Square 1 | 400 px | 11.81 ms
Square 2 | 2500 px | 15.88 ms
Square 3 | 10000 px | 28.97 ms
Square 4 | 40000 px | 86.78 ms
Square 5 | 90000 px | 159.61 ms

Test #3

Testing different image processing methods to optimize speed and the melting pool’s true

area.

There are plenty of different image filters provided by OpenCV and MATLAB. Different filters

are tried and tested for the various arguments for each function. After the filters are applied, the

area of the melting pool and the processing time are calculated. For this test, one base image was

chosen as the independent variable to keep the results consistent. The true area of the base image is calculated and compared to the areas of the filtered images. Each test is run 5 times to acquire

an average time.

A couple of important things to note about this test is that the threshold limit for each test is 215.

Meaning that any pixel value less than 215 is turned black (0) and all other pixels become white

(1). Thresholding is an essential filter to calculate the area and other parameters of the sputter.

One other important note is that only the processing time of the filters is taken, not the time it

takes to calculate the area of the sputter. This is done to isolate the impact the filters have on the

processing time because if one calculated area is bigger than another area that would affect the

processing time.

Filters used

- Gaussian Blur: reduces the image noise and the detail of an image.
- Dilate: adds pixels to the boundaries of a binary image.
- Erode: subtracts pixels from the boundaries of a binary image.
- Threshold: simplest way to create a binary image.

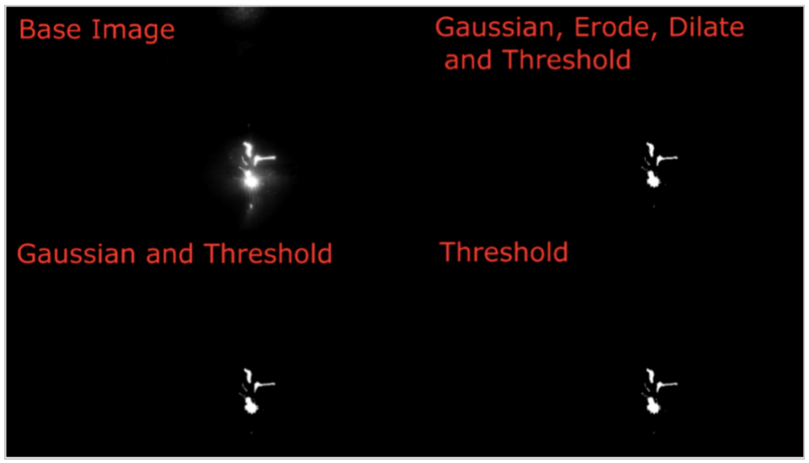
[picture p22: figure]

Figure 33: Montage of filtered images

Table 27: Filtered images processing time and area

| Area | Processing Time
Base Image | 3237 px | 0 ms
Gaussian Blur, Threshold, Dilate, and Erode | 3236 px | 11.67 ms
Gaussian Blur and Threshold | 3239 px | 7.08 ms
Threshold | 3238 px | 2.22 ms

It is seen from the results [Table 27] that filters have a negligible effect on the area of the sputter.

There is no loss in any important information from using Gaussian Blur, Dilate, and Erode. For

the final model, it was chosen to stay with thresholding.

Test #4

Showing parameters vs not showing parameters

The main focus of the project is meeting the real-time hard deadline required to process frames at

30 fps. If the system is unable to meet this deadline, then the system is useless to the sponsors.

There are various ways in which the code can be optimized without affecting the functionality of

the end-product. One way in which this is done is by eliminating the visual aspects of the

display. This means the code would still save the parameters of the main sputter (X/Y cords,

Area, Radius, and Brightness) to a file, but it would not display these parameters in real-time. To

test this, there will be three different versions of the code. One in which all the parameters and

contours are displayed, a version where only the contoured image is displayed, and a final

version where only the preprocessed image is displayed.

For this test the test model [Figure 34] will be utilized to process a live video feed. This live

video feed will be able to spit a file with the parameter, with a display window, and an extra

Simulink block that will take the fps of the processed video feed. An average fps will be taken

from the live feed and will be compared to each test.

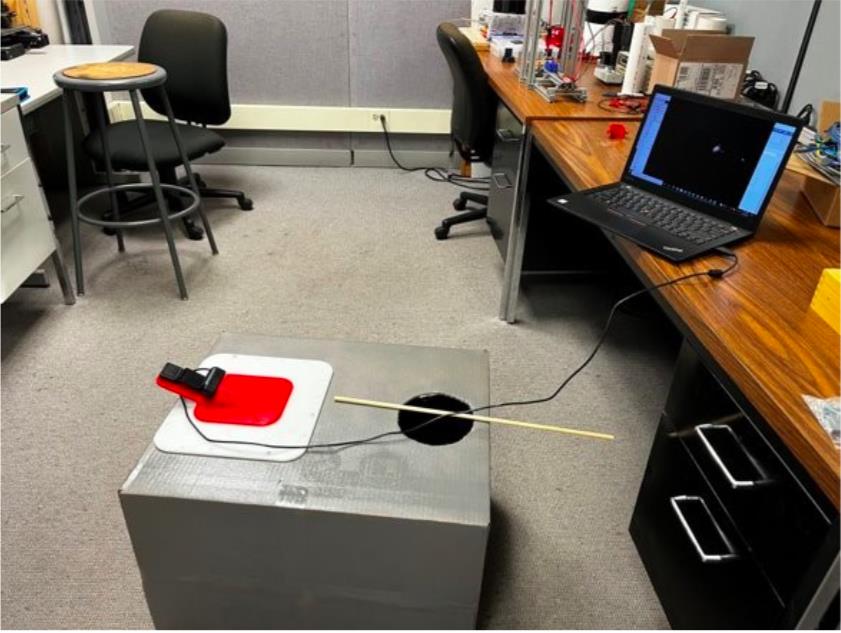
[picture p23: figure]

Figure 34: Test setup

Figure 35: Live process on the test setup

The above image [Figure 35] is from the base video without any image processing and

calculations of the parameters. Due to hardware limitations of the ThinkPad and the UVC

camera only a max of 28.28 frames per second can be achieved. The second test returns a contoured live feed and a “.mat file” at the of the test. There is only a 3 frame drop between the

first and second tests. This is not the case when showing the parameters to the user. For the third

test both the contour and parameters are shown to the user, but it greatly affects the fps of the

live feed. The parameters are already saved to a “.mat file” at the end of the test, so it does not

make sense to visually show it to the user if affects the processing time drastically. When the

code is implemented onto the real-time unit it can run 60+ fps making it impossible for any user

to read the parameters in the live feed.

Test #5

Testing the accuracy of radius measurements to verify that the code’s outputs are valid.

By printing out a copy of the splatter image to scale, the radius can be manually measured. A

ruler will be used to make the measurement. The manually measured radius data should coincide

with the data output from the system. This is needed to determine whether the code is working

properly, and that the user will receive useful data. Five tests would have been performed to

verify the accuracy of the measurements. Again, because of the hardware malfunction, this test

could not be carried out.

Test #6

Testing the portability of the system.

Each component of the system was weighed using a digital bathroom scale. Additionally, the

operator of the system documented how each part is picked up and if they meet the requirements

in the chart. If the object is less than 51 lbs. and all answers are yes/true, then the object qualifies

as an OSHA safe lift. [Table 28] The OSHA requirements are met completely.

Table 28: OSHA test requirements

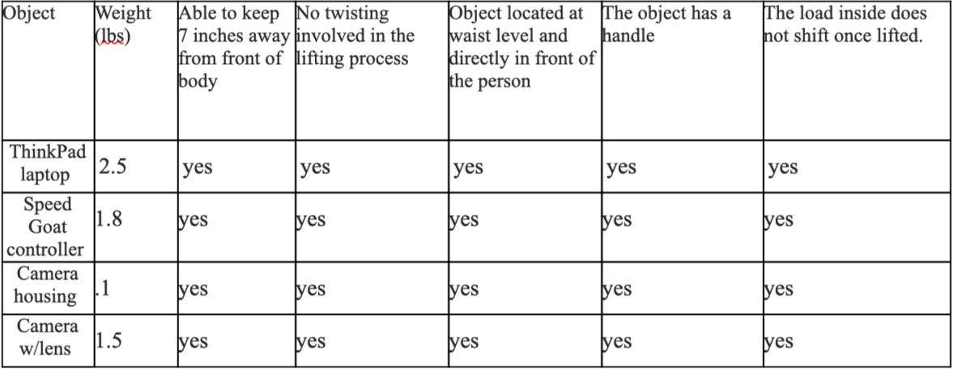
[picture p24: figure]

Test #7

Testing the consistency of the camera placement

To check the constancy of the placement of the camera, fiduciary markers would be placed into

the mock setup. The operator will rotate the camera until the markers are aligned with the

expected orientation of the system and take a screenshot of the video feed. The operator will then

remove the camera and redo the process. Software, WinMerge, will be used to compare the

pixels of the two screenshots and consistency will be noted by counting the number of

differences calculated by the software. The mock setup was not built with the exact dimensions

of the SLM printer and therefore rendered this test invalid.

### 11.3 Analysis

During this testing process, there was no raw data evaluated. All test results are shown above in

the previous section. Because of the malfunctioning hardware and limited access to the SLM

printer, there were no measurements made.
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

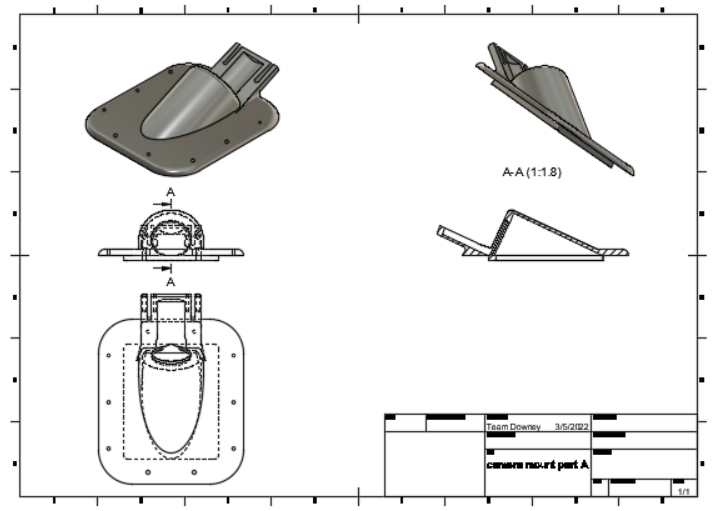
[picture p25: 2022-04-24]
CLAMS_Hardware/Custom_Camera_Mount/CAD_Drawings/Camera Mount Part A.png

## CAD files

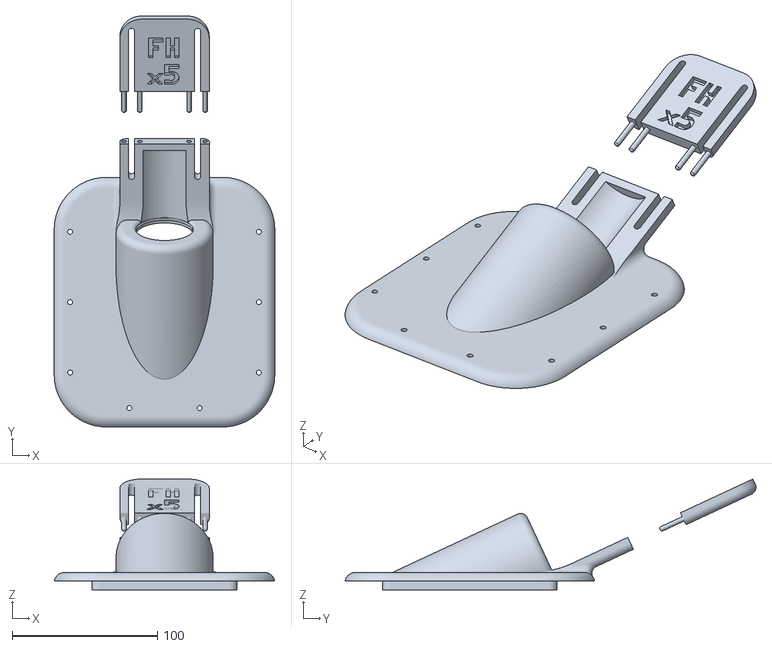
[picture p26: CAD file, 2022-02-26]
CLAMS_Hardware/Custom_Camera_Mount/CAD_Files/Version_3/flir_mount_v3.stl
152.0 x 283.1 x 76.4

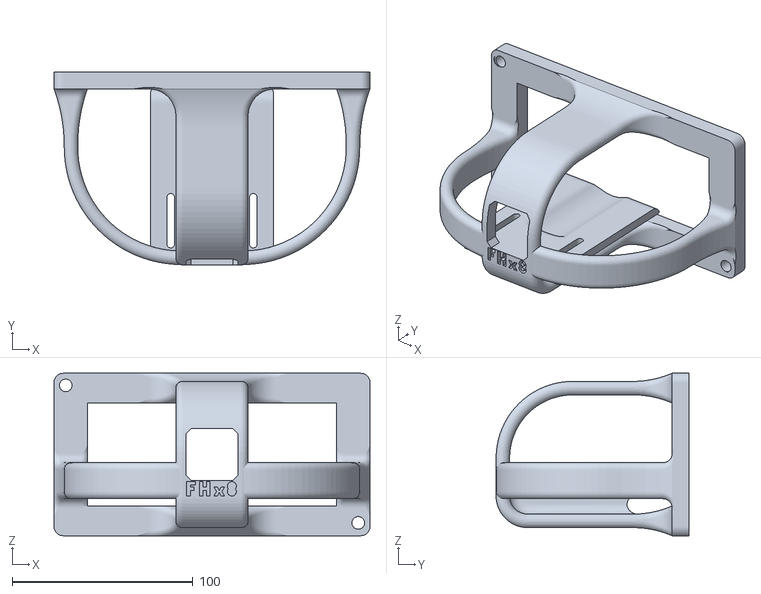
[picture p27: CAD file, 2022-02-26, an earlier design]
CLAMS_Hardware/Custom_Camera_Mount/CAD_Files/Version_2/flir_mount_v2.stl
175.0 x 106.8 x 90.0

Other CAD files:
CLAMS_Hardware/Custom_Camera_Mount/CAD_Files/Version_1/flir_mount_v1.f3d
CLAMS_Hardware/Custom_Camera_Mount/CAD_Files/Version_2/flir_mount_v2.f3d
CLAMS_Hardware/Custom_Camera_Mount/CAD_Files/Version_3/flir_mount_v3.f3d

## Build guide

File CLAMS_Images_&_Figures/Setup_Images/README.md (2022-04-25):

# Setup Images
## [Return to Images & Figures Readme](https://github.com/ARTS-Laboratory/Senior-Design-Project-EMCH427-002-Team-4-Downey/tree/main/CLAMS_Images_%26_Figures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)

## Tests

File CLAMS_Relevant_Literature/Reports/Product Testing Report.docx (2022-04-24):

Product Testing Report

Team Downey

By: Braden Priddy, Malichi Flemming,

Saif Wilkes-Davis, Tyler Owens

1. Introduction

Product testing is critical to verify the system's functionality and assess its limitations. Data must be acquired through experimentation, processed for error mitigation, and analyzed for results. For this product, the following parameters were evaluated: consistency and speed of the operating system, camera’s field of view and placement, most efficient processing method, and accurate measurements. The most rigorously tested parameters were the consistency and speed of the operating system because they fulfill the most essential requirement for real-time image processing.

Since real-time systems are defined by hard deadline times, the system would fail if these deadlines weren’t met. Henceforth, most of the testing focused on optimizing the code and the system, as well as testing the limits of the code.

Despite the end product not being functional due to a hardware malfunction of the Speed Goat, the project was a success overall. The code for the system meets the required timing deadline and processes a SLM video on a Speed Goat Real-time Unit. To demonstrate the functionality of the code, a prototype was assembled using a test setup, laptop, and a USB camera. The prototype produced a processed image and a file containing splatter parameter data on a live feed at 30 fps. The last step to completing the product is finding and configuring a Speed Goat compatible camera.

2. Test Plan

Due to limited access to the SLM printer laboratory, the construction of a rudimentary model of the SLM printer was required to conduct adequate experimentation. The model was comprised of a cardboard box, the plastic plate where the camera housing is seated, and a Styrofoam ball to imitate the metal splatter. A square hole was cut out on the top of the box which allows the camera housing to fit securely with the plastic plate and for the camera to view inside the box. A circular hole was cut out at the opposite end of the box as an area for the splatter replica to be suspended from. The inside of the box was painted black, and the splatter replica was painted bright green and illuminated with a flashlight to mimic the light contrast.

Test #1

Testing individual function processing times.

Throughout the majority of the coding process, only one frame was being processed to see if it met the sponsors’ real-time deadline of 30 milliseconds. One way this can be analyzed is looking at individual functions within the code to see which has the greatest effect on processing time. This gives an idea of what to focus on when optimizing. This test was done multiple times throughout the design process. This test is our final function time analysis test of the completed code.

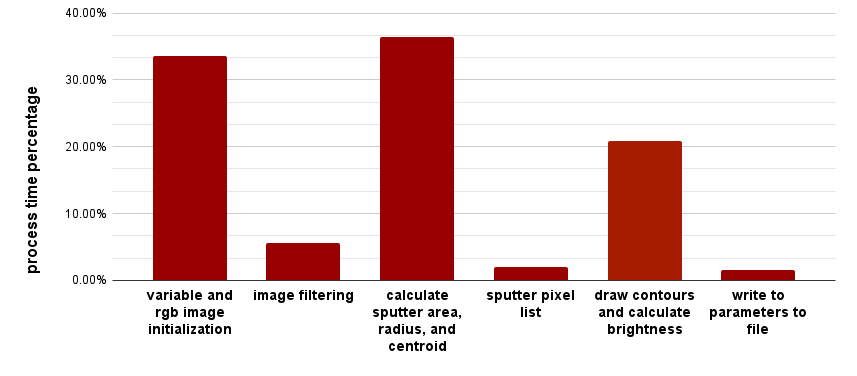
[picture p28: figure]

Figure 1: Function time analysis of a single frame

Calculating the sputter area, radius, and centroid take up the greatest percentage of the processing time. These calculations are done using the MATLAB function “regionprops”, very little was done to optimize this as calculating the radius and centroid is difficult. The next most expensive function is the “variable and RGB image initialization”, this cannot be optimized further as the minimum number of variables is already used. The last function that takes a large percentage of the processing time is the “draw contours and calculate the brightness”. This can be optimized by no longer drawing the contour around the image, but this eliminates visual aspect of our display which tells the user that the sputter is being found by the code. The reason this function takes so long is that the code must go through the entire sputter pixel list to calculate the brightness.

Test #2

Testing frames per second vs the size of melting sputter.

The code must calculate the brightness and the contours of the main sputter. As the sputter gets bigger the more pixels, we must go through to calculate these parameters. For this test, 5 white squares of increasing size show how each affects the processing time. From this test, the limits of the code were visualized. The code must work at 30 fps and the processing time needs to work under 33 milliseconds.

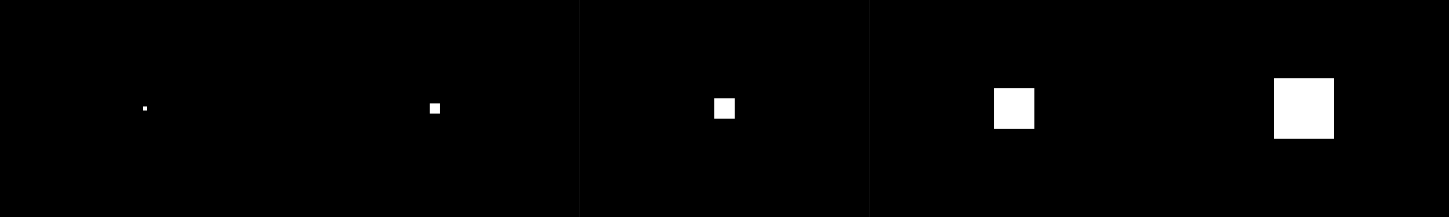
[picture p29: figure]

Figure 2: Five 1440x1080 images of squares

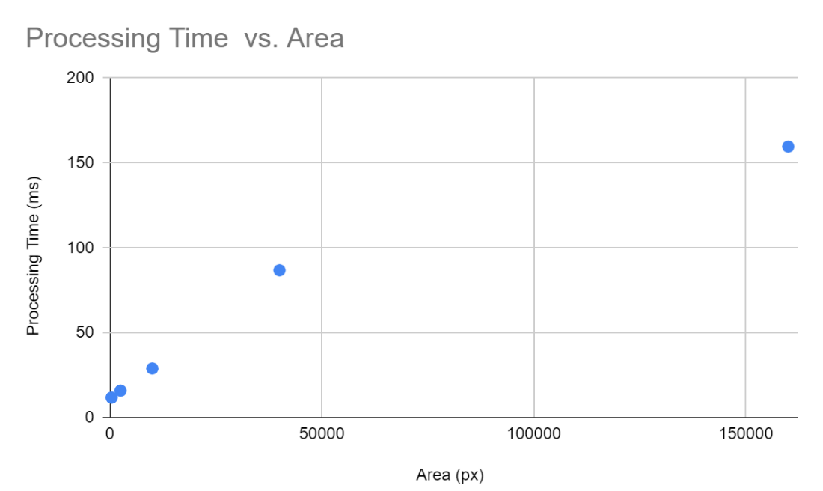
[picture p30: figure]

Figure 3: Processing time vs. Area

Table 1: Processing time vs. Area of squares

| Area | Processing Time
Square 1 | 400 px | 11.81 ms
Square 2 | 2500 px | 15.88 ms
Square 3 | 10000 px | 28.97 ms
Square 4 | 40000 px | 86.78 ms
Square 5 | 90000 px | 159.61 ms

Test #3

Testing different image processing methods to optimize speed and the melting pool’s true area.

There are plenty of different image filters provided by OpenCV and MATLAB. Different filters are tried and tested for the various arguments for each function. After the filters are applied, the area of the melting pool and the processing time are calculated. For this test, one base image was chosen as the independent variable to keep the results consistent. The true area of the base image is calculated and compared to the areas of the filtered images. Each test is run 5 times to acquire an average time.

A couple of important things to note about this test is that the threshold limit for each test is 215. Meaning that any pixel value less than 215 is turned black (0) and all other pixels become white (1). Thresholding is an essential filter to calculate the area and other parameters of the sputter. One other important note is that only the processing time of the filters is taken, not the time it takes to calculate the area of the sputter. This is done to isolate the impact the filters have on the processing time because if one calculated area is bigger than another area that would affect the processing time.

Filters used

- Gaussian Blur: reduces the image noise and the detail of an image.
- Dilate: adds pixels to the boundaries of a binary image.
- Erode: subtracts pixels from the boundaries of a binary image.
- Threshold: simplest way to create a binary image.

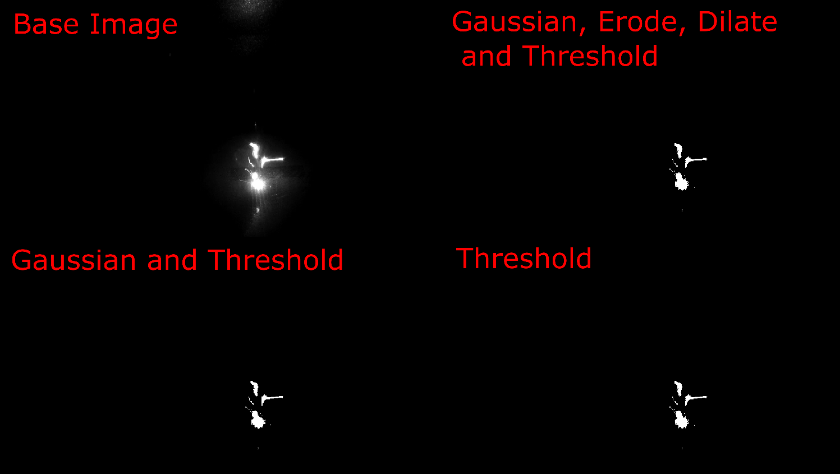
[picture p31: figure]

Figure 4: Montage of filtered images

Table 2: Filtered images processing time and area

| Area | Processing Time
Base Image | 3237 px | 0 ms
Gaussian Blur, Threshold, Dilate, and Erode | 3236 px | 11.67 ms
Gaussian Blur and Threshold | 3239 px | 7.08 ms
Threshold | 3238 px | 2.22 ms

It is seen from the results that filters have a negligible effect on the area of the sputter. There is no loss in any important information from using Gaussian Blur, Dilate, and Erode. For the final model, it was chosen to stay with thresholding.

Test #4

Showing parameters vs not showing parameters

The main focus of the project is meeting the real-time hard deadline required to process frames at 30 fps. If the system is unable to meet this deadline, then our system is useless to the sponsors. There are various ways in which the code can be optimized without affecting the functionality of the end product. One way in which this is done is by eliminating the visual aspects of the display. This means the code would still save the parameters of the main sputter (X/Y cords, Area, Radius, and Brightness) to a file, but it would not display these parameters in real-time. To test this, there will be three different versions of the code. One in which all the parameters and contours are displayed, a version where only the contoured image is displayed, and a final version where only the preprocessed image is displayed.

For this test the test model will be utilized to process a live video feed. This live video feed will be able to spit a file with the parameter, with a display window, and an extra Simulink block that will take the fps of the processed video feed. An average fps will be taken from the live feed and will be compared to each test.

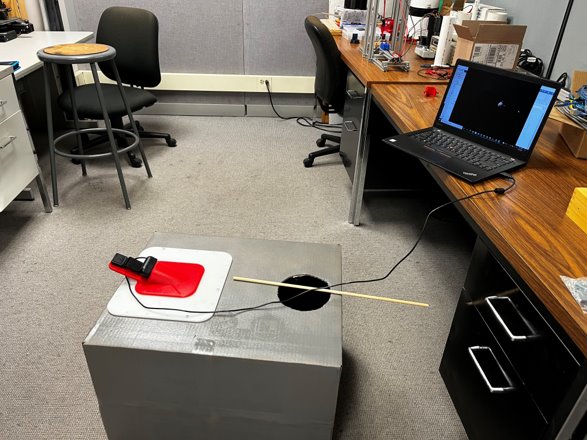
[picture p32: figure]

Figure 5: Test mock setup

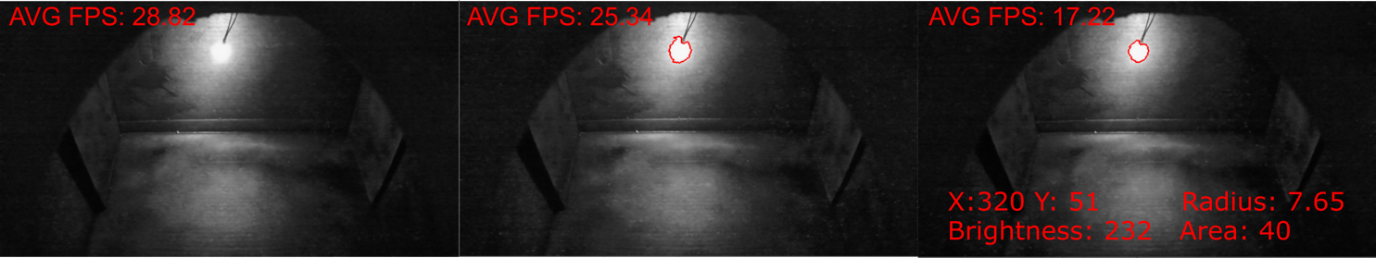
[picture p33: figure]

Figure 6: Live process on the test setup

The first image [Figure 6] is from the base video without any image processing and calculations of the parameters. Due to hardware limitations of the ThinkPad and the UVC camera only a max of 28.28 frames per second can be achieved. The second test returns a contoured live feed and a “.mat file” at the of the test. There is only a roughly 3 frame drop between the first and second tests. This is not the case when showing the parameters to the user. For the third test both the contour and parameters are shown to the user, but it greatly affects the fps of the live feed. The parameters are already saved to a “.mat file” at the end of the test, so it does not make sense to visually show it to the user if affects the processing time drastically. When the code is implemented onto the real-time unit it can run 60+ fps making it impossible for any user to read the parameters in the live feed.

Test #5

Testing the accuracy of radius measurements to verify that the code’s outputs are valid.

By printing out a copy of the splatter image to scale, the radius can be manually measured. A ruler will be used to make the measurement. The manually measured radius data should coincide with the data output from the system. This is needed to determine whether the code is working properly, and that the user will receive useful data. Five tests would have been performed to verify the accuracy of the measurements. Again, because of the hardware malfunction, this test could not be carried out.

Test #6

Testing the portability of the system.

Each component of the system will be weighed using a digital bathroom scale. Additionally, the operator of the system will document how each part is picked up and if they meet the requirements in the chart. If the object is less than 51 lbs. and all answers are yes/true, then the object qualifies as an OSHA safe lift. [Table 3] The OSHA requirements are met completely.

Table 3: OSHA test requirements

Object | Weight (lbs) | Able to keep 7 inches away from front of body | No twisting involved in the lifting process | Object located at waist level and directly in front of the person | The object has a handle | The load inside does not shift once lifted.
ThinkPad laptop | 2.5 | yes | yes | yes | yes | yes
Speed Goat controller | 1.8 | yes | yes | yes | yes | yes
Camera housing | .1 | yes | yes | yes | yes | yes
Camera w/lens | 1.5 | yes | yes | yes | yes | yes

Test #7

Testing the consistency of the camera placement

To check the constancy of the placement of the camera, fiduciary markers would be placed into the mock setup. The operator will rotate the camera until the markers are aligned with the expected orientation of the system and take a screenshot of the video feed. The operator will then remove the camera and redo the process. Software, WinMerge, will be used to compare the pixels of the two screenshots and consistency will be noted by counting the number of differences calculated by the software. The mock setup was not built with the exact dimensions of the SLM printer and therefore rendered this test invalid.

3. Analysis

During this testing process, there was no raw data evaluated. All test results are shown above in the previous section. Because of the malfunctioning hardware and limited access to the SLM printer, there were no measurements made.

4. Conclusions/Recommendations:

Five tests were performed on this system to check for processing time, frames per second, speed optimization, consistency of parameters, and OSHA compliancy. The results for these tests were satisfactory and met the target values. However, there were two tests that were not performed because of the hardware malfunction prior to beginning the tests and the lack of access to the SLM printer. These would have evaluated the accuracy of measurements being made by the system along with the consistency of the camera’s field of view. For future testing, having a fully functional control system and full access to the SLM printer is highly recommended.

EMCH 428Team DowneyUniversity of South Carolina

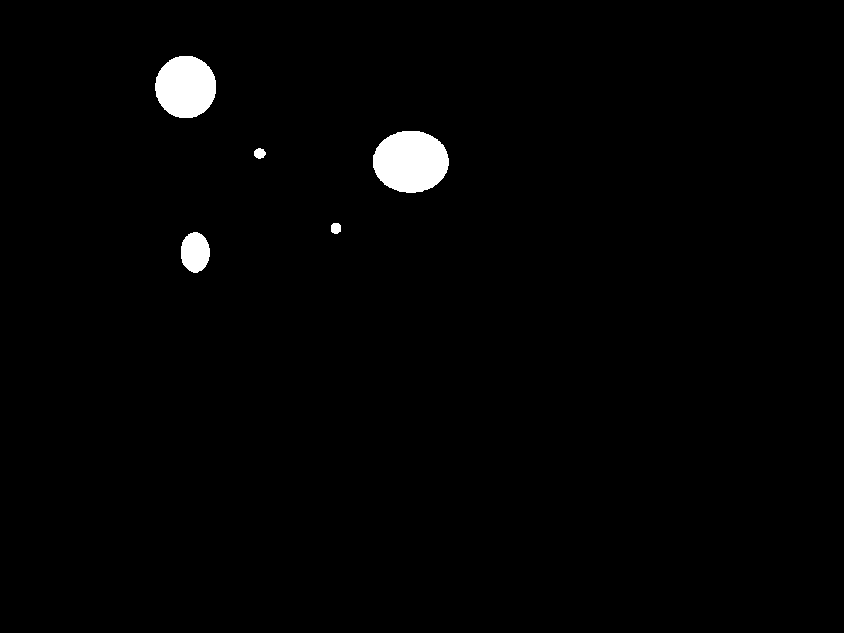
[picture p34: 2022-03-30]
CLAMS_Images_&_Figures/Test_Images/test2.png

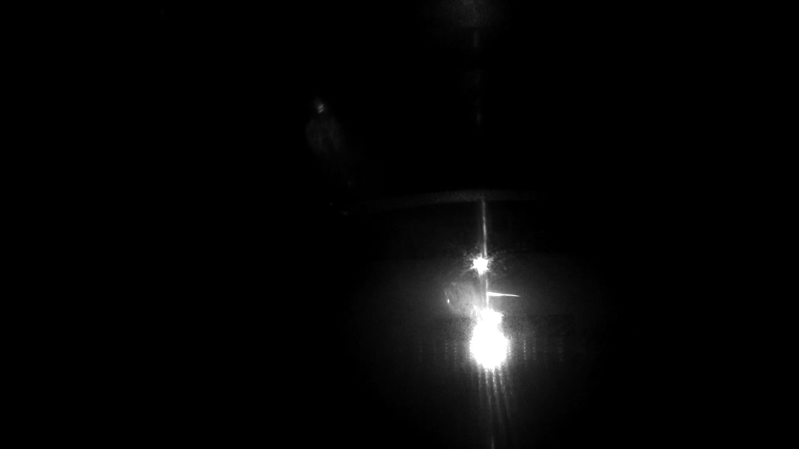
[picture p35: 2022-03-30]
CLAMS_Images_&_Figures/Edited_Test_Images/FILR_edit4.jpg

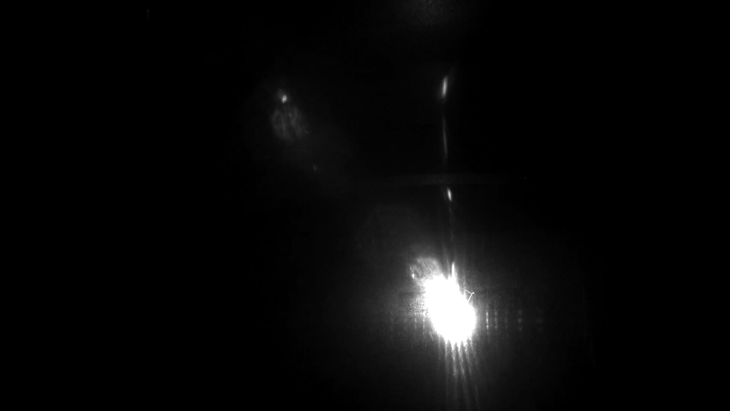
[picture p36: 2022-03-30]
CLAMS_Images_&_Figures/Edited_Test_Images/FILR_edit12.jpg

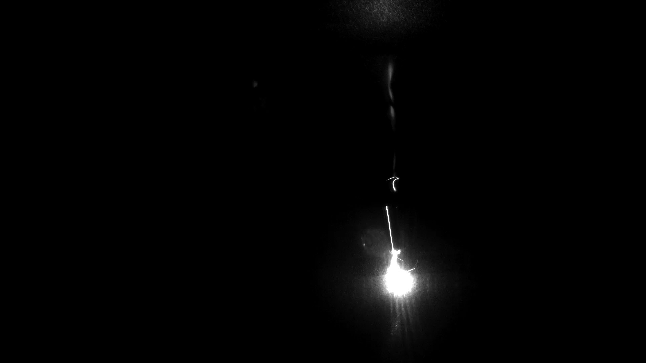
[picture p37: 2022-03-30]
CLAMS_Images_&_Figures/Edited_Test_Images/FILR_edit7.jpg

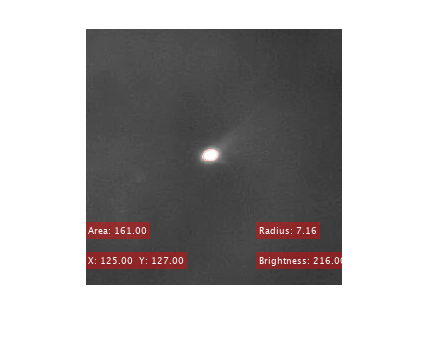
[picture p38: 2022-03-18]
CLAMS_Images_&_Figures/Processed_Test_Images/test_processed_frame.png

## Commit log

2021-09-03 update
    This repository contains software and hardware files for Camera-in-the-loop System for Additive Manufacturing
2021-09-03 Create CAD files
2022-02-26 malichi update
    [flir_mount_v1.f3d, flir_mount_v2.f3d, flir_mount_v2.stl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]
2022-03-02 Updated Python Function
    Processes the frames of the SLM process
2022-03-09 Spring Break Updates
    optimized and implemented matlab code into simulink
2022-04-23 malichi updates
    [flir_mount_v1.f3d, flir_mount_v2.f3d, flir_mount_v2.stl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]
